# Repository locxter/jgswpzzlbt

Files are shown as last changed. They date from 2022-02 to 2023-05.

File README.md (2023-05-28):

# jgswpzzlbt

## Overview

> This project is **DEPRECATED**, therefore might not be on par with my current coding standards and will not receive any updates now or in the future.

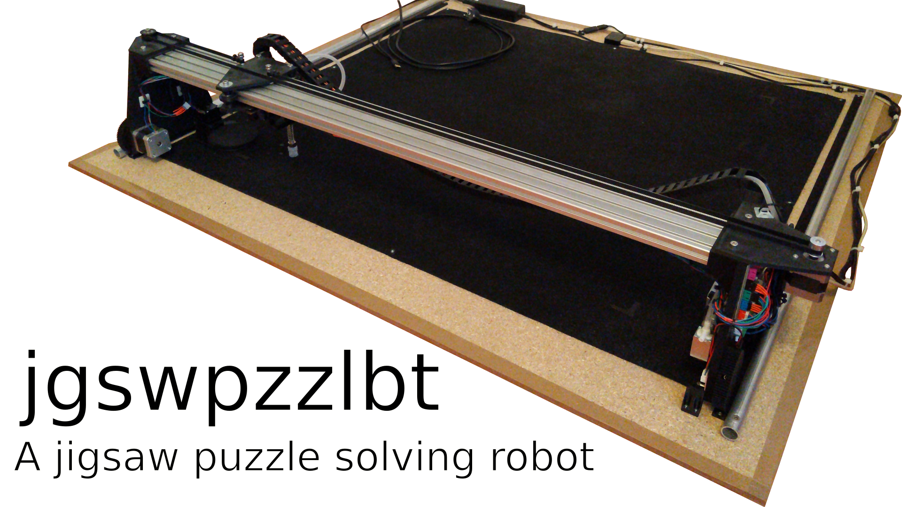
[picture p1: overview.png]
Overview image


This is a jigsaw puzzle solving robot I designed. It is programmed in C++ using OpenCV for image recognition and LibSerial for communicating with a custom Arduino firmware. For further information take a look at the overview video `overview.mp4` or the result images `6-part-result.jpeg` and `24-part-result.jpeg`.

## Dependencies

I generally try to minimize dependencies, but I'm a one man crew and can therefore only support Debian-based Linux distributions as I'm running one myself. Anyway, you need to have the following packages installed for everything to work properly:

- FreeCAD for editing and exporting the CAD files. Install it with `sudo apt install freecad`.
- A2Plus for assemblying the different components in FreeCAD. Install it via the integrated addon manager.
- freecad.gears for creating the needed gears in FreeCAD. Install it via the integrated addon manager.
- Arduino IDE as a way to compile the Arduino code. Install it with `sudo apt install arduino`.
- GCC, G++, GDB and CMake for building the C++ code. Install them with `sudo apt install build-essential gdb cmake`.
- OpenCV as the used computer vision library. Install it with `sudo apt install libopencv-dev`.
- LibSerial as the used serial communication library. Install it with `sudo apt install libserial-dev`.

## How it works

The process of solving a jigsaw puzzle automatically involves the following major steps:

1. Locating the somewhat randomly positioned parts.
2. Creating detailed pictures of all the parts.
3. Moving the parts to known positions inside a predefined matrix.
4. Locating each part in the provided overview picture of the puzzle.
5. Translating the digital positions to a real world ones.
6. Moving all the pieces to their final position.

## How to build it

jgswpzzlbt's mechanics mainly consist of a big 110x120cm chipboard, a 1m long 20x80mm aluminium extrusion and some custom 3D printed parts. For further information take a look at the assembly overview image `cad/assembly.png` as well as the assembly overview CAD model `cad/assembly.FCStd`. But please don't expect any parts to fit perfectly or be easy to assamble as only one prototype has been build so far.

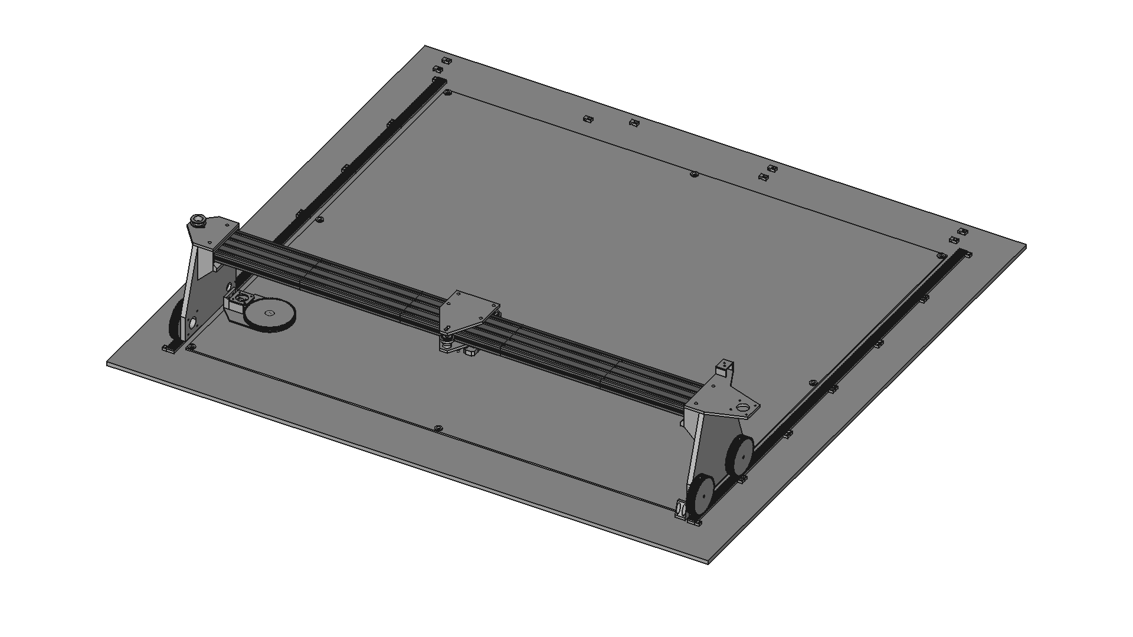
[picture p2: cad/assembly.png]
Assembly image


Below is a full bill of materials with German sources for all non printable parts:

| Quantity: | Item: | Source: |
| --- | --- | --- |
| 1 | MKS Base motherboard | [Amazon](https://www.amazon.de/Base-V1-6-RepRap-3D-Drucker-Steuerung/dp/B07G9K1T28) |
| 1 | HBV-1716WA USB camera | [Amazon](https://www.amazon.de/USB-Kameramodul-HBV-1716WA-Millionen-Weitwinkelobjektiv-OV2710-Chip/dp/B07QXXFGSM) |
| 1 | USB extension | [Amazon](https://www.amazon.de/deleyCON-Speed-Verl%C3%A4ngerungskabel-Stecker-Buchse/dp/B00WHZ7GBW) |
| 3 | NEMA 17 1.8deg stepper motor | [Amazon](https://www.amazon.de/STEPPERONLINE-Schrittmotor-63-74oz-4-Draht-Stepper/dp/B07MZJGNZN) |
| 1 | NEMA 11 1.8deg stepper motor | [Amazon](https://www.amazon.de/STEPPERONLINE-Schrittmotor-Bipolar-28x28x31mm-DRUCKER/dp/B07HHZQMDW) |
| 1 | Power supply | [Amazon](https://www.amazon.de/Netzteil-Netzadapter-Transformator-Kaltger%C3%A4testecker-Streifen/dp/B07FNMKTBL) |
| 1 | SG90 micro servo | [Amazon](https://www.amazon.de/ARCELI-Flugzeug-Zubeh%C3%B6r-Arduino-Hubschrauber/dp/B07MY2Y253) |
| 2 | Endstop | [Amazon](https://www.amazon.de/GTIWUNG-Mechanischer-Endschalter-3D-Drucker-Makerbot/dp/B07VWRS24K) |
| 1 | Vacuum pump | [Amazon](https://www.amazon.de/KSTE-Vakuumpumpe-Mikrovakuumpumpe-Mini-Luftpumpe-Behandlungsinstrument/dp/B08BJWLKBW) |
| 1 | Vacuum nozzle | [Amazon](https://www.amazon.de/SRJQXH-Pneumatischer-TS-M10-L80-11-Saugnapfhalter-Industrieller/dp/B098SCMZWY) |
| 1 | Vacuum valve | [Amazon](https://www.amazon.de/Magnetventil-%C3%96ffner-Fl%C3%BCssigkeit-Pneumatik-Elektroventil/dp/B0858Y2KSG) |
| 1 | Vacuum tubing | [Amazon](https://www.amazon.de/JBL-Luftschlauch-Länge-Durchmesser-Aquaschlauch/dp/B000H6SRMU) |
| 1 | Vacuum tubing connectors | [Amazon](https://www.amazon.de/Uniclife-Aquariumschl%C3%A4uche-Luftschlauchverbinder-Kunststoff-St%C3%BCck/dp/B07Q9Q9C8Y) |
| 1 | GT2 belt | [Amazon](https://www.amazon.de/OZUAR-Zahnriemen-3D-Drucker-Breite-Abstand/dp/B07D4GCYXW) |
| 1 | Cable ties and cable tie mounts | [Amazon](https://www.amazon.de/Hipeqia-Nylon-Kabelbinder-Kabelbinderhalter-Selbstklebend-Hitzebest%C3%A4ndig/dp/B08CL2JFCH) |
| 1 | Double sided tape | [Amazon](https://www.amazon.de/doppelseitiges-Klebeband-klebend-verschiedene-Breiten/dp/B00G6SCYCM) |
| 1 | Instant glue | [Amazon](https://www.amazon.de/Pattex-Sekundenkleber-L%C3%B6sungsmittelfreier-Gel-Kleber-Transparent/dp/B00O23B8IE) |
| 1 | Cable chain | [Amazon](https://www.amazon.de/Haobase-Plastic-Towline-Cable-Chain/dp/B06XKZ35VH) |
| 1 | Cables | [Amazon](https://www.amazon.de/Donau-Elektronik-GMBH-Original-Kupfer/dp/B01BI1G88C) |
| 1 | Pin header | [Amazon](https://www.amazon.de/IZOKEE-Männlich-Stiftleiste-Buchsenleiste-Lochrasterplatine/dp/B07DBY753C) |
| 1 | Jigsaw puzzle mat | [Amazon](https://www.amazon.de/maDDma-Bastelfilz-Meterware-Taschenfilz-Filzstoff/dp/B0797QR4LL) |
| 1 | 110x120cm chipboard 8mm | [Globus Baumarkt](https://www.globus-baumarkt.de/spanplatte-roh-8-mm) |
| 42 | 3x12mm TX10 wood screw | [Globus Baumarkt](https://www.globus-baumarkt.de/detail/index/sArticle/27670/fs/116194815/sCategory/47135) |
| 1 | Aluminium profile 20x80 I-type slot 5 1000mm | [Motedis](https://www.motedis.com/shop/Aluprofile/20-I-Typ-Nut-5/Aluprofil-20x80-I-Typ-Nut-5::3798.html) |
| 8 | M5 t-nut I-type groove 5 | [Motedis](https://www.motedis.com/shop/Nutprofil-Zubehoer/In-der-Nut/Nutenstein-Glatt-I-Typ-Nut-5-M5::5846.html) |
| 1 | GT2 motor pulley 20 teeth, 5mm bore | [Motedis](https://www.motedis.com/shop/Dynamik/Zahnriemen-und-Zahnraeder/GT2-Riemenscheibe-20-Zaehne-5mm-Bohrung-fuer-6mm-Riemen::4248.html) |
| 11 | 625 2RS ball bearing | [Motedis](https://www.motedis.com/shop/Dynamik-Basiselemente/Kugellager/Rillenkugellager/Rillenkugellager-625-2RS-5x16x5::4290.html) |
| 4 | DIN 912 M2x20 screw | [Schraubenkasten](https://www.schraubenkasten.de/din-912-mit-innensechskant/m2-8-8-galvanisch-verzinkt-zylinderschraube_200581_13656) |
| 4 | DIN 934 M2x0.4 nut | [Schraubenkasten](https://www.schraubenkasten.de/muttern/sechskantmutter/din-934/edelstahl-a2_202500_23008) |
| 4 | DIN 912 M2.5x8 screw | [Schraubenkasten](https://www.schraubenkasten.de/din-912-mit-innensechskant/m2-5-8-8-galvanisch-verzinkt-zylinderschraube_200582_13676) |
| 32 | DIN 912 M3x8 screw | [Schraubenkasten](https://www.schraubenkasten.de/din-912-mit-innensechskant/m3-8-8-galvanisch-verzinkt-zylinderschraube_200583_13715) |
| 18 | DIN 934 M3x0.5 nut | [Schraubenkasten](https://www.schraubenkasten.de/muttern/sechskantmutter/din-934/edelstahl-a2_202502_23016) |
| 12 | DIN 912 M5x14 screw | [Schraubenkasten](https://www.schraubenkasten.de/din-912-mit-innensechskant/m5-8-8-galvanisch-verzinkt-zylinderschraube_200585_13871) |
| 5 | DIN 912 M5x25 screw | [Schraubenkasten](https://www.schraubenkasten.de/din-912-mit-innensechskant/m5-8-8-galvanisch-verzinkt-zylinderschraube_200585_13883) |
| 3 | DIN 912 M5x50 screw | [Schraubenkasten](https://www.schraubenkasten.de/din-912-mit-innensechskant/m5-8-8-galvanisch-verzinkt-zylinderschraube_200585_13899) |
| 16 | DIN 934 M5 nut | [Schraubenkasten](https://www.schraubenkasten.de/muttern/sechskantmutter/din-934/edelstahl-a2_202504_23024) |
| 3 | DIN 7349 M5 washer | [Schraubenkasten](https://www.schraubenkasten.de/scheiben/unterlegscheiben/din-7349-schweren-spannstift/5-3-din-7349-scheiben-schrauben-mit-spannstifte-a2-edelstahl_203612_23840) |
| 9 | Cable clip | 3D printer |
| 8 | Cable tie mount | 3D printer |
| 1 | C axis gear | 3D printer |
| 1 | C axis motor mount | 3D printer |
| 1 | C axis turntable | 3D printer |
| 8 | Puzzle mat clamp | 3D printer |
| 1 | Vacuum tube fitting | 3D printer |
| 1 | X axis bottom carriage | 3D printer |
| 4 | X axis camera spacer | 3D printer |
| 1 | X axis motor mount | 3D printer |
| 1 | X axis pulley | 3D printer |
| 1 | X axis pulley mount | 3D printer |
| 1 | X axis pulley spacer | 3D printer |
| 3 | X axis roller | 3D printer |
| 6 | X axis roller spacer | 3D printer |
| 1 | X axis top carriage | 3D printer |
| 2 | Y axis carriage | 3D printer |
| 4 | Y axis gear | 3D printer |
| 1 | Y axis stop | 3D printer |
| 12 | Y axis track | 3D printer |
| 1 | Z axis carriage | 3D printer |
| 1 | Z axis gear | 3D printer |
| 1 | Z axis motor mount | 3D printer |

All parts were printed on my Sovol SV01 in standard PLA with a custom super fast profile. The following settings have been used with great success:

- 0.3mm layer height
- 0.6mm line width
- 1.2mm wall thickness
- 0.9mm top/bottom tickness
- 20% line infill
- 215°C nozzle temperature
- 60°C build plate temperature
- 75mm/s print speed (37.5mm/s for the initial layer, 75mm/s for infill, 37.5mm/s for walls, 120mm for travel)
- 100% cooling from the second layer on
- Zig zag support and 5mm raft, where necessary

## How to create a jigsaw puzzle

As this robot uses a special simplified type of jigsaw puzzles, you have to create the puzzles to solve with it yourself. You can simply use the given example puzzle by going to a photo shop (they offer a way better print quality than an average home printer), printing the file(s) `reference-with-cutting-lines.png` or in case of the 24 part version `reference-with-cutting-lines-NUMBER.png` in the common 15x10cm format and cutting it into pieces. But creating your own puzzle entirely isn't to difficult either. To do so you need to create a reference image of the whole jigsaw puzzle, a variant of this image with cutting lines as well as part images to help with labeling the cut parts later on. Then just print it out in your desired size and cut it into pieces. Keep in mind that the parts shouldn't get to small to work properly, 5x5cm per part is optimal.

## How to use it

After installing all the necessary tools and libraries mentioned above as well as building the hardware, you can flash the firmware to the MKS Base motherboard via the Arduino IDE and compile the camera calibration, manual control and main program with CMake. To do so simply create a build directory in each program's folder via `mkdir build`, move to it via `cd build` and run CMake via `cmake ..` followed by make via `make`. Then test the whole system with the manual control program via `./manual-control`. If everything works correctly, the next step is to perform the automatic camera calibration via `./camera-calibration`. Finally you can run the dang awesome thing with the main software via `./software` to solve some puzzles! Have fun ;)

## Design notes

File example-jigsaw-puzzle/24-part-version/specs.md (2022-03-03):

# Specs

- Columns: 6
- Rows: 4
- Width: 30cm
- Height: 20cm

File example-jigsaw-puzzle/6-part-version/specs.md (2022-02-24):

# Specs

- Columns: 3
- Rows: 2
- Width: 15cm
- Height: 10cm

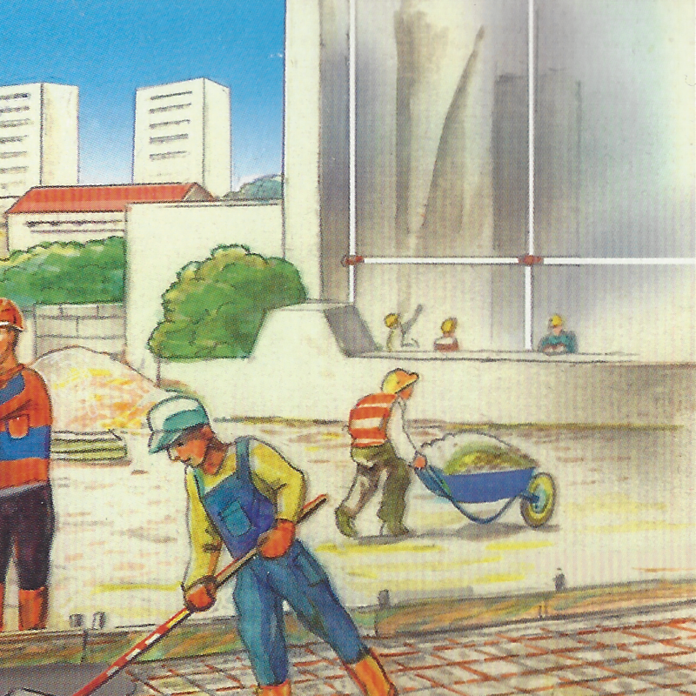
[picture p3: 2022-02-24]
example-jigsaw-puzzle/6-part-version/part-2-1.png

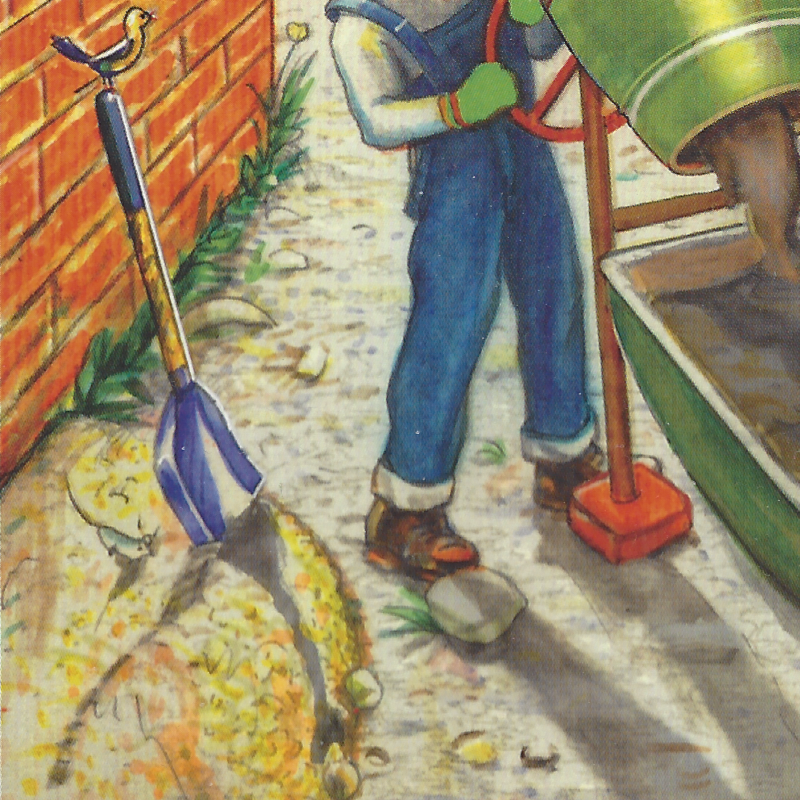
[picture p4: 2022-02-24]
example-jigsaw-puzzle/6-part-version/part-0-0.png

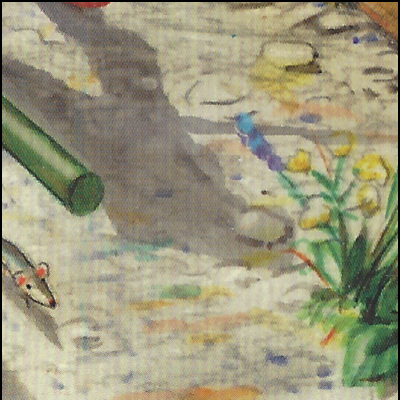
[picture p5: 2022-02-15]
example-jigsaw-puzzle/24-part-version/part-3-0.png

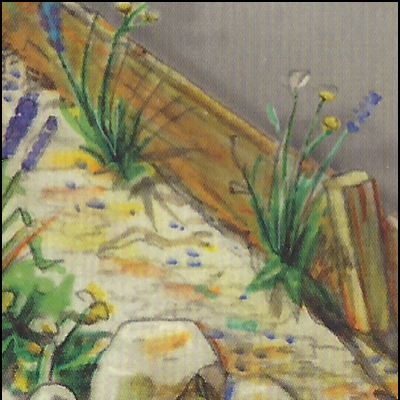
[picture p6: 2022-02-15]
example-jigsaw-puzzle/24-part-version/part-4-0.png

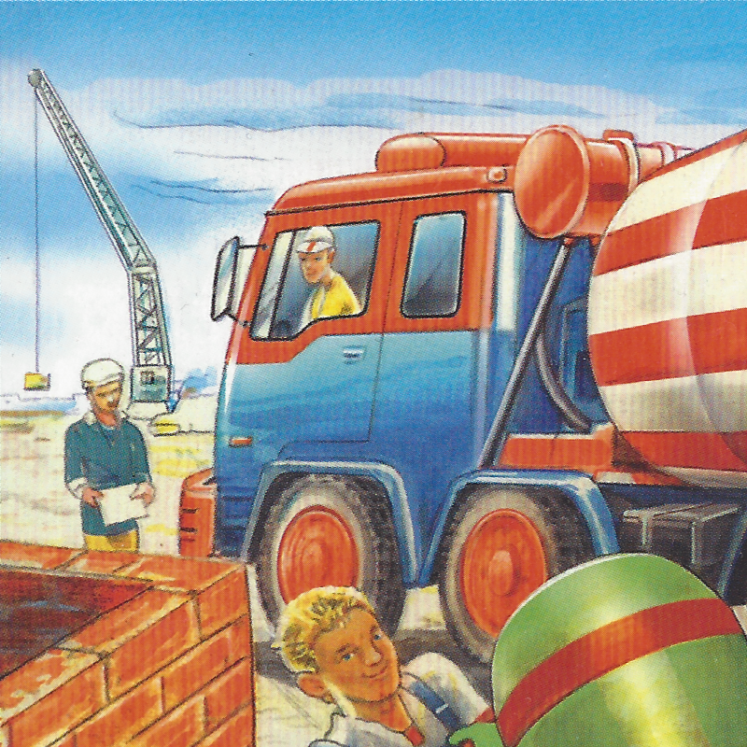
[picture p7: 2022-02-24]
example-jigsaw-puzzle/6-part-version/part-0-1.png

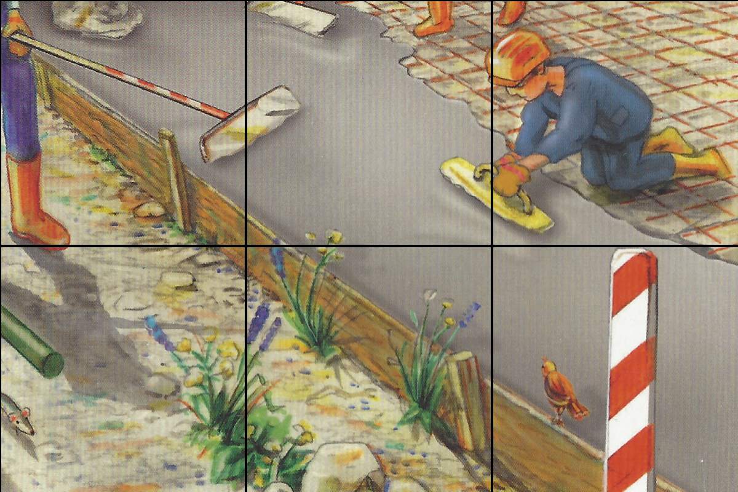
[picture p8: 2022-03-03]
example-jigsaw-puzzle/24-part-version/reference-with-cutting-lines-4.png

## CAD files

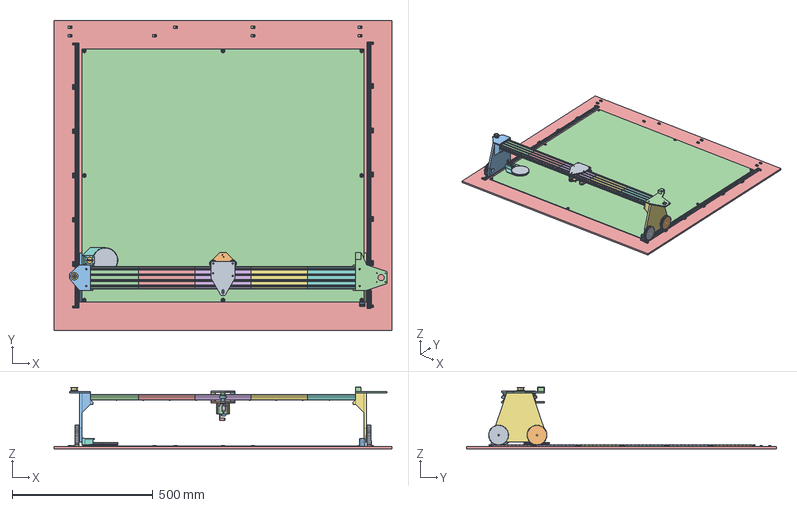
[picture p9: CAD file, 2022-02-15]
cad/assembly.FCStd
1200.0 x 1100.0 x 220.0 mm
y-axis-gear_001
y-axis-gear_002
y-axis-carriage_001
aluminium-profile1_001
aluminium-profile1_002
aluminium-profile1_003
aluminium-profile1_004
aluminium-profile1_005
y-axis-gear_003
y-axis-gear_004
x-axis-pulley-mount_001
x-axis-motor-mount_001
cable-clip_001
cable-clip_002
cable-clip_003
cable-clip_004
cable-clip_005
cable-clip_006
cable-clip_007
cable-clip_008
cable-clip_009
x-axis-pulley-spacer_001
x-axis-pulley_001
x-axis-roller_001
x-axis-roller_002
x-axis-roller_003
x-axis-roller-spacer_001
x-axis-roller-spacer_002
x-axis-roller-spacer_003
x-axis-roller-spacer_004
x-axis-roller-spacer_005
x-axis-roller-spacer_006
x-axis-top-carriage_001
x-axis-bottom-carriage_001
x-axis-camera-spacer_001
x-axis-camera-spacer_002
x-axis-camera-spacer_003
x-axis-camera-spacer_004
y-axis-track_001
y-axis-track_002
y-axis-track_003
y-axis-track_004
y-axis-track_005
y-axis-track_006
y-axis-track_007
y-axis-track_008
y-axis-track_009
y-axis-track_010
y-axis-track_011
y-axis-track_012
cable-tie-mount_001
cable-tie-mount_002
cable-tie-mount_003
cable-tie-mount_004
cable-tie-mount_005
cable-tie-mount_006
cable-tie-mount_007
cable-tie-mount_008
puzzle-mat-clamp_001
puzzle-mat-clamp_002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

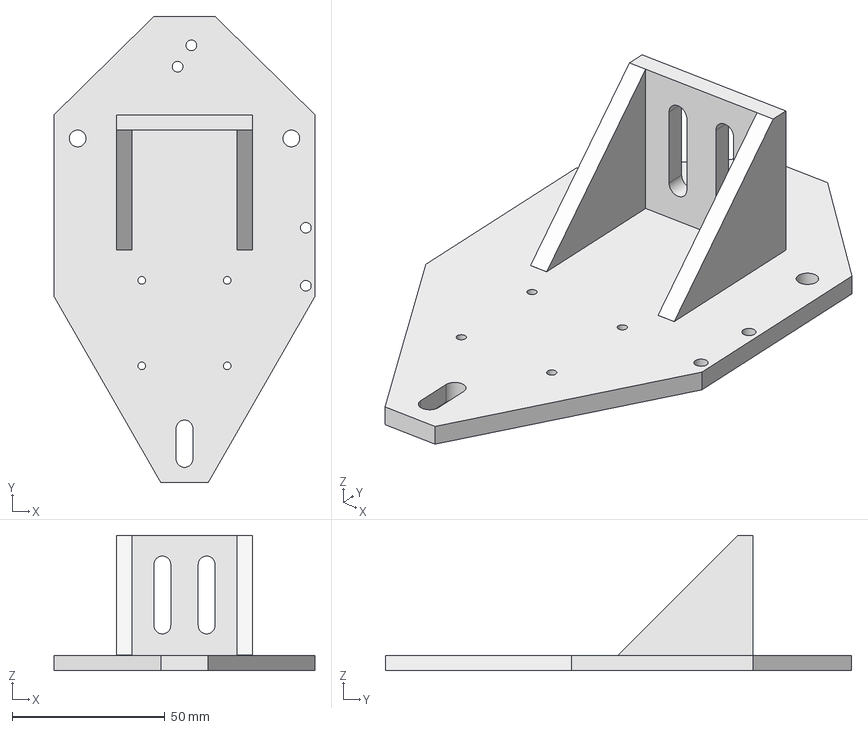
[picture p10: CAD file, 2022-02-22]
cad/x-axis-bottom-carriage.FCStd
85.5 x 152.7 x 44.3 mm

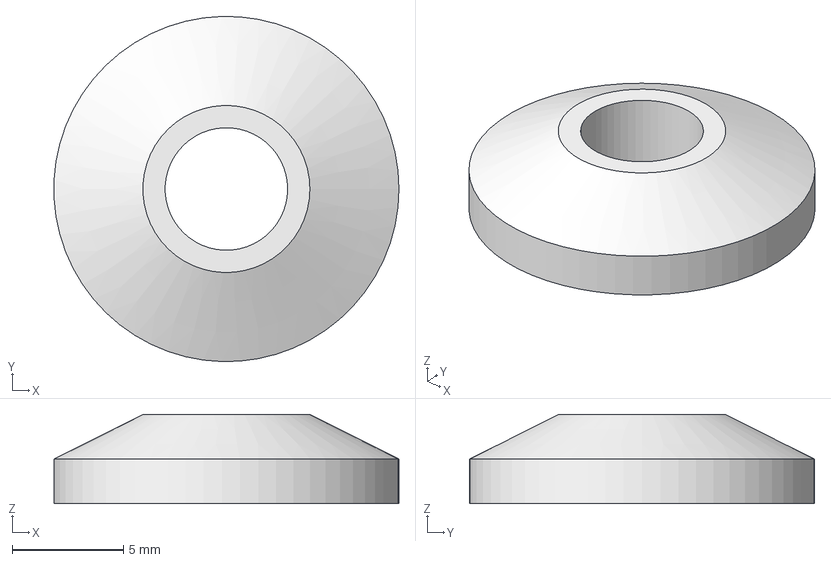
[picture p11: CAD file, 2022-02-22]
cad/x-axis-pulley-spacer.FCStd
15.5 x 15.5 x 4.00 mm

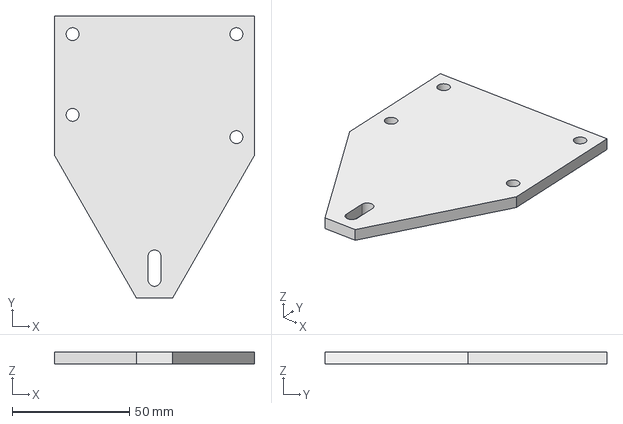
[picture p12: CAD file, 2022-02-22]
cad/x-axis-top-carriage.FCStd
85.5 x 120.5 x 5.00 mm

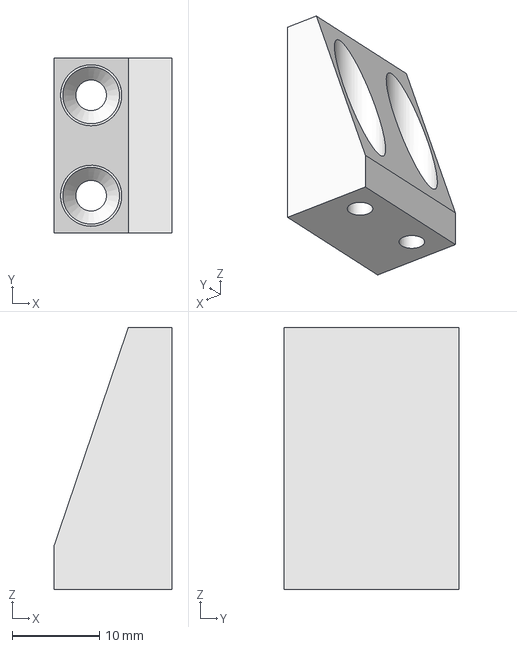
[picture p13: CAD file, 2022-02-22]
cad/y-axis-stop.FCStd
13.5 x 20.0 x 30.0 mm

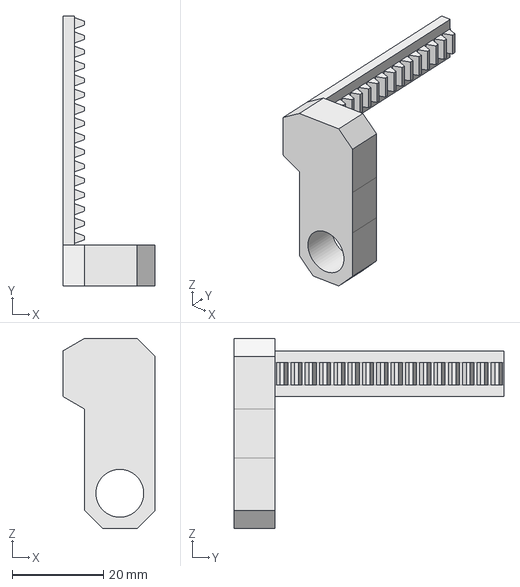
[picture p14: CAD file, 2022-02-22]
cad/z-axis-carriage.FCStd
20.2 x 59.3 x 41.8 mm

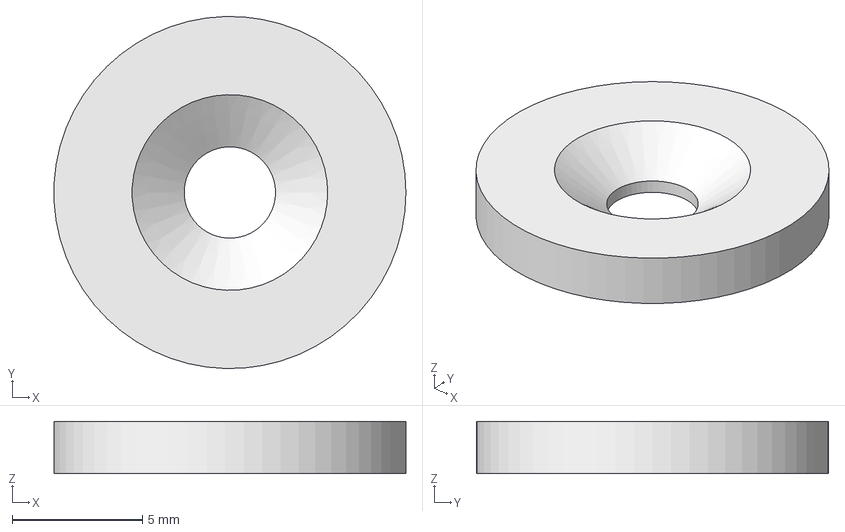
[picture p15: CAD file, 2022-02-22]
cad/puzzle-mat-clamp.FCStd
13.5 x 13.5 x 2.00 mm

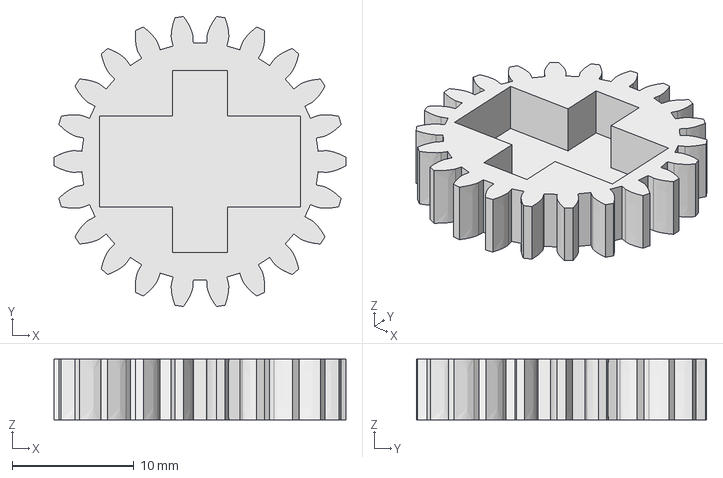
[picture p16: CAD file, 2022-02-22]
cad/z-axis-gear.FCStd
24.0 x 23.8 x 5.00 mm

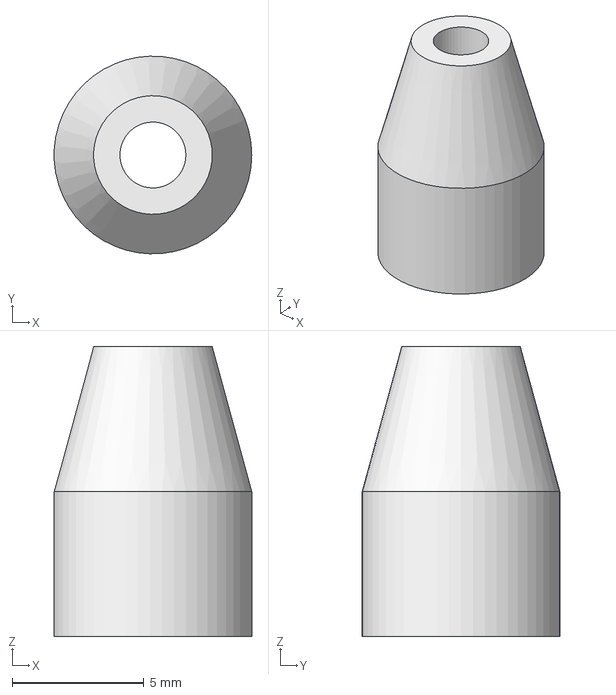
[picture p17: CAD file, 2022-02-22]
cad/x-axis-camera-spacer.FCStd
7.49 x 7.50 x 11.0 mm

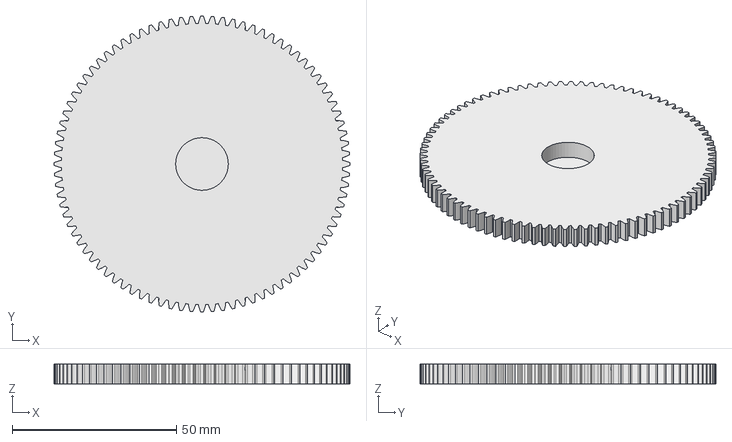
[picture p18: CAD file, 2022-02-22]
cad/c-axis-turntable.FCStd
90.0 x 90.0 x 6.00 mm

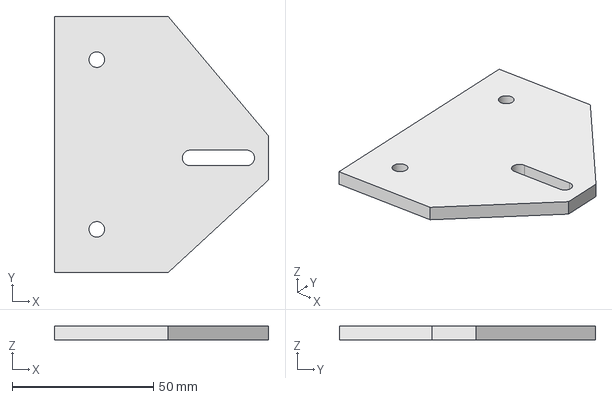
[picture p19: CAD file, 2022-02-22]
cad/x-axis-pulley-mount.FCStd
75.8 x 90.5 x 5.00 mm

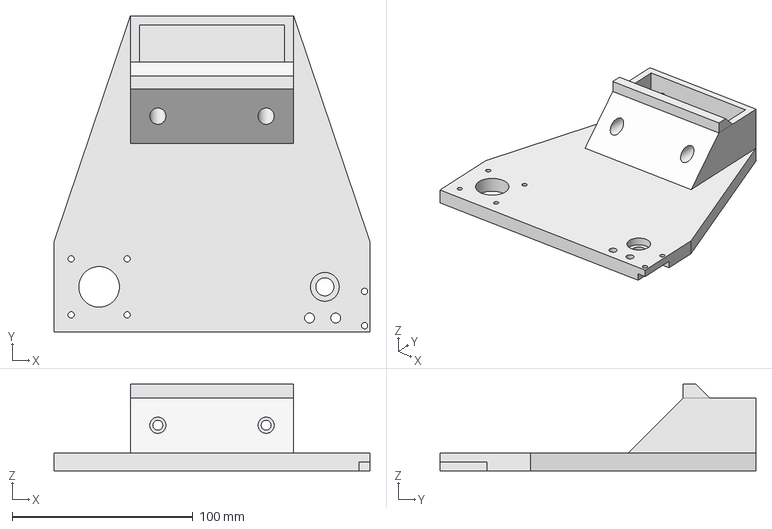
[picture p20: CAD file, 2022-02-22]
cad/y-axis-carriage.FCStd
175.0 x 175.0 x 48.0 mm

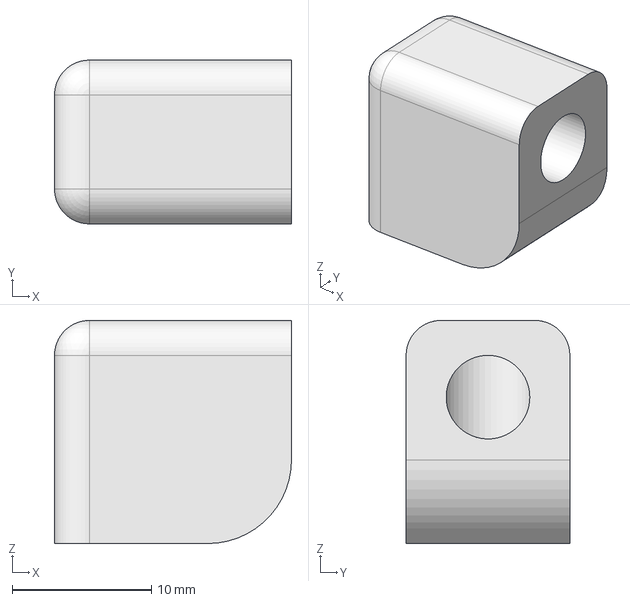
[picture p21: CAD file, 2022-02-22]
cad/vacuum-tube-fitting.FCStd
17.0 x 11.8 x 16.0 mm

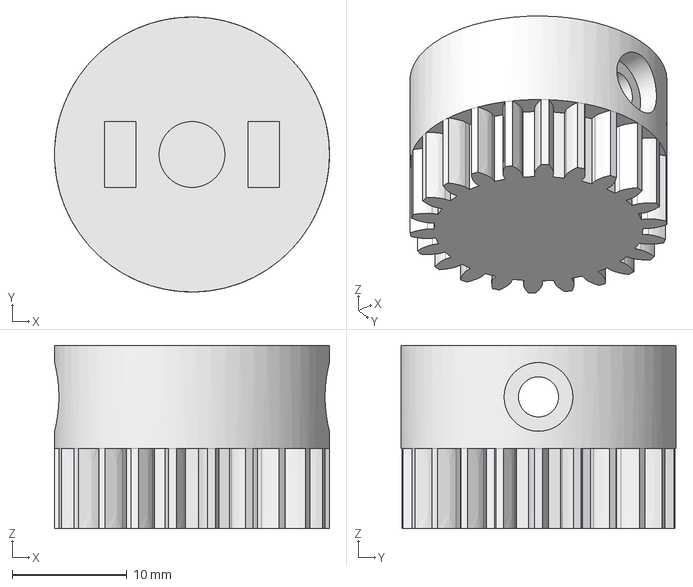
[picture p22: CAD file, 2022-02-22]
cad/c-axis-gear.FCStd
24.0 x 24.0 x 16.0 mm

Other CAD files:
cad/y-axis-track.FCStd
cad/y-axis-gear.FCStd
cad/x-axis-motor-mount.FCStd
cad/cable-tie-mount.FCStd
cad/aluminium-profile.stp
cad/c-axis-gear.stl
cad/c-axis-motor-mount.FCStd
cad/c-axis-motor-mount.stl
cad/c-axis-servo-arm.stl
cad/c-axis-turntable.stl
cad/cable-clip.FCStd
cad/cable-clip.stl
cad/puzzle-mat-clamp.stl
cad/vacuum-tube-fitting.stl
cad/x-axis-bottom-carriage.stl
cad/x-axis-camera-spacer.stl
cad/x-axis-motor-mount.stl
cad/x-axis-pulley-mount.stl
cad/x-axis-pulley-spacer.stl
cad/x-axis-pulley.FCStd
cad/x-axis-pulley.stl
cad/x-axis-roller-spacer.FCStd
cad/x-axis-roller-spacer.stl
cad/x-axis-roller.FCStd
cad/x-axis-roller.stl
cad/x-axis-top-carriage.stl
cad/y-axis-carriage.stl
cad/y-axis-gear.stl
cad/y-axis-stop.stl
cad/y-axis-track.stl
cad/z-axis-carriage.stl
cad/z-axis-gear.stl
cad/z-axis-motor-mount.FCStd
cad/z-axis-motor-mount.stl

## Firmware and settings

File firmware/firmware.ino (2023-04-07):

#include <Servo.h>

// Pins
const int X_AXIS_STP_PIN = A0;
const int X_AXIS_DIR_PIN = A1;
const int Y_AXIS_0_STP_PIN = A6;
const int Y_AXIS_0_DIR_PIN = A7;
const int Y_AXIS_1_STP_PIN = 46;
const int Y_AXIS_1_DIR_PIN = 48;
const int C_AXIS_STP_PIN = 26;
const int C_AXIS_DIR_PIN = 28;
const int X_AXIS_ENDSTOP_PIN = 3;
const int Y_AXIS_ENDSTOP_PIN = 14;
const int VACUUM_PUMP_PIN = 8;
const int VACUUM_VALVE_PIN = 10;

// Serial messages
const char AVAILABILITY_MESSAGE = 'R';
const char ERROR_MESSAGE = 'E';

// Servo object
Servo servo;

// Minimum x, y and c axis step intervals
const int X_AXIS_STEP_INTERVAL = 150;
const int Y_AXIS_STEP_INTERVAL = 750;
const int C_AXIS_STEP_INTERVAL = 200;

// Maximum x, y and z axis coordinates
const int X_AXIS_MAX = 825;
const int Y_AXIS_MAX = 725;
const int Z_AXIS_MAX = 90;

// X and y axis movement per rotation
const int X_AXIS_MOVEMENT_PER_ROTATION = 40;
const int Y_AXIS_MOVEMENT_PER_ROTATION = 220;

// Own functions
void homeAxis();
void moveXAxis(int x);
void moveYAxis(int y);
void moveZAxis(int z);
void moveCAxis(int angle);
void controlVacuumSystem(bool isOn);

// Setup function
void setup() {
    // More pins
    const int X_AXIS_ENA_PIN = 38;
    const int X_AXIS_MS1_PIN = 5;
    const int X_AXIS_MS2_PIN = 6;
    const int Y_AXIS_0_ENA_PIN = A2;
    const int Y_AXIS_0_MS1_PIN = A5;
    const int Y_AXIS_0_MS2_PIN = A4;
    const int Y_AXIS_1_ENA_PIN = A8;
    const int Y_AXIS_1_MS1_PIN = 22;
    const int Y_AXIS_1_MS2_PIN = 39;
    const int C_AXIS_ENA_PIN = 24;
    const int C_AXIS_MS1_PIN = A9;
    const int C_AXIS_MS2_PIN = A10;
    const int SERVO_PIN = 11;
    // Initiate pins and set them to their default states
    pinMode(X_AXIS_STP_PIN, OUTPUT);
    digitalWrite(X_AXIS_STP_PIN, LOW);
    pinMode(X_AXIS_DIR_PIN, OUTPUT);
    digitalWrite(X_AXIS_DIR_PIN, LOW);
    pinMode(X_AXIS_ENA_PIN, OUTPUT);
    digitalWrite(X_AXIS_ENA_PIN, LOW);
    pinMode(X_AXIS_MS1_PIN, OUTPUT);
    digitalWrite(X_AXIS_MS1_PIN, HIGH);
    pinMode(X_AXIS_MS2_PIN, OUTPUT);
    digitalWrite(X_AXIS_MS2_PIN, HIGH);
    pinMode(Y_AXIS_0_STP_PIN, OUTPUT);
    digitalWrite(Y_AXIS_0_STP_PIN, LOW);
    pinMode(Y_AXIS_0_DIR_PIN, OUTPUT);
    digitalWrite(Y_AXIS_0_DIR_PIN, HIGH);
    pinMode(Y_AXIS_0_ENA_PIN, OUTPUT);
    digitalWrite(Y_AXIS_0_ENA_PIN, LOW);
    pinMode(Y_AXIS_0_MS1_PIN, OUTPUT);
    digitalWrite(Y_AXIS_0_MS1_PIN, HIGH);
    pinMode(Y_AXIS_0_MS2_PIN, OUTPUT);
    digitalWrite(Y_AXIS_0_MS2_PIN, HIGH);
    pinMode(Y_AXIS_1_STP_PIN, OUTPUT);
    digitalWrite(Y_AXIS_1_STP_PIN, LOW);
    pinMode(Y_AXIS_1_DIR_PIN, OUTPUT);
    digitalWrite(Y_AXIS_1_DIR_PIN, LOW);
    pinMode(Y_AXIS_1_ENA_PIN, OUTPUT);
    digitalWrite(Y_AXIS_1_ENA_PIN, LOW);
    pinMode(Y_AXIS_1_MS1_PIN, OUTPUT);
    digitalWrite(Y_AXIS_1_MS1_PIN, HIGH);
    pinMode(Y_AXIS_1_MS2_PIN, OUTPUT);
    digitalWrite(Y_AXIS_1_MS2_PIN, HIGH);
    pinMode(C_AXIS_STP_PIN, OUTPUT);
    digitalWrite(C_AXIS_STP_PIN, LOW);
    pinMode(C_AXIS_DIR_PIN, OUTPUT);
    digitalWrite(C_AXIS_DIR_PIN, LOW);
    pinMode(C_AXIS_ENA_PIN, OUTPUT);
    digitalWrite(C_AXIS_ENA_PIN, LOW);
    pinMode(C_AXIS_MS1_PIN, OUTPUT);
    digitalWrite(C_AXIS_MS1_PIN, HIGH);
    pinMode(C_AXIS_MS2_PIN, OUTPUT);
    digitalWrite(C_AXIS_MS2_PIN, HIGH);
    pinMode(X_AXIS_ENDSTOP_PIN, INPUT);
    pinMode(Y_AXIS_ENDSTOP_PIN, INPUT);
    pinMode(VACUUM_PUMP_PIN, OUTPUT);
    digitalWrite(VACUUM_PUMP_PIN, LOW);
    pinMode(VACUUM_VALVE_PIN, OUTPUT);
    digitalWrite(VACUUM_VALVE_PIN, LOW);
    servo.attach(SERVO_PIN);
    // Open the serial connection
    Serial.begin(115200);
    // Home robot
    homeAxis();
}

// Main function
void loop() {
    // Check for new serial data
    if (Serial.available()) {
        // More serial messages
        const char X_AXIS_COMMAND = 'X';
        const char Y_AXIS_COMMAND = 'Y';
        const char Z_AXIS_COMMAND = 'Z';
        const char C_AXIS_COMMAND = 'C';
        const char VACUUM_SYSTEM_COMMAND = 'V';
        // Reade commands and their according parameters
        String input = Serial.readStringUntil('\n');
        char command = input.charAt(0);
        int commandParameter = input.substring(1).toInt();
        // Execute known commands or print an error
        switch (command) {
            case X_AXIS_COMMAND:
                moveXAxis(commandParameter);
                break;
            case Y_AXIS_COMMAND:
                moveYAxis(commandParameter);
                break;
            case Z_AXIS_COMMAND:
                moveZAxis(commandParameter);
                break;
            case C_AXIS_COMMAND:
                moveCAxis(commandParameter);
                break;
            case VACUUM_SYSTEM_COMMAND:
                if (commandParameter < 1) {
                    controlVacuumSystem(false);
                } else {
                    controlVacuumSystem(true);
                }
                break;
            default:
                Serial.print(ERROR_MESSAGE);
                Serial.print('\n');
                break;
        }
    }
}

// Function for homing the robot
void homeAxis() {
    // Variables for storing time before homing the x or y axis and success of that operation
    unsigned long startAxisHoming;
    bool success = true;
    // Move servo to a deactive coordinate
    if (servo.read() != Z_AXIS_MAX) {
        servo.write(Z_AXIS_MAX);
    }
    // Home the x axis
    startAxisHoming = millis();
    digitalWrite(X_AXIS_DIR_PIN, !digitalRead(X_AXIS_DIR_PIN));
    while (digitalRead(X_AXIS_ENDSTOP_PIN) == HIGH) {
        digitalWrite(X_AXIS_STP_PIN, HIGH);
        delayMicroseconds(10);
        digitalWrite(X_AXIS_STP_PIN, LOW);
        delayMicroseconds((2 * X_AXIS_STEP_INTERVAL) - 10);
        if (millis() - startAxisHoming > 60000) {
            success = false;
            break;
        }
    }
    digitalWrite(X_AXIS_DIR_PIN, !digitalRead(X_AXIS_DIR_PIN));
    // Home the y axis
    startAxisHoming = millis();
    digitalWrite(Y_AXIS_0_DIR_PIN, !digitalRead(Y_AXIS_0_DIR_PIN));
    digitalWrite(Y_AXIS_1_DIR_PIN, !digitalRead(Y_AXIS_1_DIR_PIN));
    while (digitalRead(Y_AXIS_ENDSTOP_PIN) == HIGH) {
        digitalWrite(Y_AXIS_0_STP_PIN, HIGH);
        digitalWrite(Y_AXIS_1_STP_PIN, HIGH);
        delayMicroseconds(10);
        digitalWrite(Y_AXIS_0_STP_PIN, LOW);
        digitalWrite(Y_AXIS_1_STP_PIN, LOW);
        delayMicroseconds((2 * Y_AXIS_STEP_INTERVAL) - 10);
        if (millis() - startAxisHoming > 60000) {
            success = false;
            break;
        }
    }
    digitalWrite(Y_AXIS_0_DIR_PIN, !digitalRead(Y_AXIS_0_DIR_PIN));
    digitalWrite(Y_AXIS_1_DIR_PIN, !digitalRead(Y_AXIS_1_DIR_PIN));
    // Check for homing error and print an according message
    if (success) {
        Serial.print(AVAILABILITY_MESSAGE);
        Serial.print('\n');
    } else {
        Serial.print(ERROR_MESSAGE);
        Serial.print('\n');
    }
}

// Function for controlling the x axis motor
void moveXAxis(int x) {
    // Variable to store current coordinate
    static int currentX = 0;
    // Limiting the parameter range
    if (x > X_AXIS_MAX) {
        x = X_AXIS_MAX;
    } else if (x < 0) {
        x = 0;
    }
    // Controlling the motor
    if (x != currentX) {
        int mmToGo;
        unsigned long long stepsToGo;
        // Calculating step interval related variables
        const long MAX_STEP_INTERVAL = (long) 100 * X_AXIS_STEP_INTERVAL;
        const long MIN_STEP_INTERVAL = X_AXIS_STEP_INTERVAL;
        const float STEP_INTERVAL_CHANGE = ((float) MAX_STEP_INTERVAL - MIN_STEP_INTERVAL) / 200;
        // Choosing a movement direction
        if (x > currentX) {
            mmToGo = x - currentX;
        } else if (x < currentX) {
            mmToGo = currentX - x;
            digitalWrite(X_AXIS_DIR_PIN, !digitalRead(X_AXIS_DIR_PIN));
        }
        stepsToGo = round(((float) mmToGo / X_AXIS_MOVEMENT_PER_ROTATION) * 3200);
        // Sending the step signals
        for (unsigned long long i = 0; i < stepsToGo; i++) {
            long stepInterval = MIN_STEP_INTERVAL - 10;
            // Slowing down at the start and end of the move
            if (i < 201) {
                stepInterval = round(MAX_STEP_INTERVAL - (i * STEP_INTERVAL_CHANGE)) - 10;
            } else if (i > (stepsToGo - 201)) {
                stepInterval = round(MIN_STEP_INTERVAL + ((i - (stepsToGo - 200)) * STEP_INTERVAL_CHANGE)) - 10;
            }
            digitalWrite(X_AXIS_STP_PIN, HIGH);
            delayMicroseconds(10);
            digitalWrite(X_AXIS_STP_PIN, LOW);
            delayMicroseconds(stepInterval);
        }
        // Resetting the movement direction
        if (x < currentX) {
            digitalWrite(X_AXIS_DIR_PIN, !digitalRead(X_AXIS_DIR_PIN));
        }
        // Updating the known x coordinate
        currentX = x;
    }
    // Printing an availability message
    Serial.print(AVAILABILITY_MESSAGE);
    Serial.print('\n');
}

// Function for controlling the y axis motor
void moveYAxis(int y) {
    // Defining variable to store current coordinate
    static int currentY = 0;
    // Limiting the parameter range
    if (y > Y_AXIS_MAX) {
        y = Y_AXIS_MAX;
    } else if (y < 0) {
        y = 0;
    }
    // Controlling the motor
    if (y != currentY) {
        int mmToGo;
        unsigned long long stepsToGo;
        // Choosing a movement direction
        if (y > currentY) {
            mmToGo = y - currentY;
        } else if (y < currentY) {
            mmToGo = currentY - y;
            digitalWrite(Y_AXIS_0_DIR_PIN, !digitalRead(Y_AXIS_0_DIR_PIN));
            digitalWrite(Y_AXIS_1_DIR_PIN, !digitalRead(Y_AXIS_1_DIR_PIN));
        }
        stepsToGo = round(((float) mmToGo / Y_AXIS_MOVEMENT_PER_ROTATION) * 3200);
        // Sending the step signals
        for (unsigned long long i = 0; i < stepsToGo; i++) {
            long stepInterval = Y_AXIS_STEP_INTERVAL - 10;
            // Slowing down at the start and end of the move
            if (i < 201 || i > (stepsToGo - 201)) {
                stepInterval = (2 * Y_AXIS_STEP_INTERVAL) - 10;
            }
            digitalWrite(Y_AXIS_0_STP_PIN, HIGH);
            digitalWrite(Y_AXIS_1_STP_PIN, HIGH);
            delayMicroseconds(10);
            digitalWrite(Y_AXIS_0_STP_PIN, LOW);
            digitalWrite(Y_AXIS_1_STP_PIN, LOW);
            delayMicroseconds(stepInterval);
        }
        // Resetting the movement direction
        if (y < currentY) {
            digitalWrite(Y_AXIS_0_DIR_PIN, !digitalRead(Y_AXIS_0_DIR_PIN));
            digitalWrite(Y_AXIS_1_DIR_PIN, !digitalRead(Y_AXIS_1_DIR_PIN));
        }
        // Updating the known y coordinate
        currentY = y;
    }
    // Printing an availability message
    Serial.print(AVAILABILITY_MESSAGE);
    Serial.print('\n');
}

// Function for controlling the x axis servo
void moveZAxis(int z) {
    // Limiting the parameter range
    if (z > Z_AXIS_MAX) {
        z = Z_AXIS_MAX;
    } else if (z < 0) {
        z = 0;
    }
    // Controlling the servo
    if (z != servo.read()) {
        servo.write(z);
    }
    // Printing an availability message
    Serial.print(AVAILABILITY_MESSAGE);
    Serial.print('\n');
}

// Function for controlling the c axis motor
void moveCAxis(int angle) {
    unsigned long long stepsToGo = round((abs(angle) / 90.0) * 3200);
    // Calculating step interval related variables
    const long MAX_STEP_INTERVAL = 100 * C_AXIS_STEP_INTERVAL;
    const long MIN_STEP_INTERVAL = C_AXIS_STEP_INTERVAL;
    const float STEP_INTERVAL_CHANGE = ((float) MAX_STEP_INTERVAL - MIN_STEP_INTERVAL) / 200;
    // Choosing a movement direction
    if (angle < 0) {
        digitalWrite(C_AXIS_DIR_PIN, !digitalRead(C_AXIS_DIR_PIN));
    }
    // Sending the step signals
    for (unsigned long long i = 0; i < stepsToGo; i++) {
        long stepInterval = MIN_STEP_INTERVAL - 10;
        // Slowing down at the start and end of the move
        if (i < 201) {
            stepInterval = round(MAX_STEP_INTERVAL - (i * STEP_INTERVAL_CHANGE)) - 10;
        } else if (i > (stepsToGo - 201)) {
            stepInterval = round(MIN_STEP_INTERVAL + ((i - (stepsToGo - 200)) * STEP_INTERVAL_CHANGE)) - 10;
        }
        digitalWrite(C_AXIS_STP_PIN, HIGH);
        delayMicroseconds(10);
        digitalWrite(C_AXIS_STP_PIN, LOW);
        delayMicroseconds(stepInterval);
    }
    // Resetting the movement direction
    if (angle < 0) {
        digitalWrite(C_AXIS_DIR_PIN, !digitalRead(C_AXIS_DIR_PIN));
    }
    // Printing an availability message
    Serial.print(AVAILABILITY_MESSAGE);
    Serial.print('\n');
}

// Function for controlling the vacuum system
void controlVacuumSystem(bool isOn) {
    // Controlling the vacuum system
    if (isOn) {
        digitalWrite(VACUUM_VALVE_PIN, LOW);
        digitalWrite(VACUUM_PUMP_PIN, HIGH);
    } else {
        digitalWrite(VACUUM_VALVE_PIN, HIGH);
        digitalWrite(VACUUM_PUMP_PIN, LOW);
    }
    // Printing an availability message
    Serial.print(AVAILABILITY_MESSAGE);
    Serial.print('\n');
}

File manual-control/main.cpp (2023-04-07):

#include "lib/libserial-helpers.hpp"
#include "lib/opencv-helpers.hpp"
#include <iostream>

// Main function
int main(int argc, char** argv) {
    // Check for the right number of command line arguments
    if (argc == 4) {
        // Variables for command line arguments
        const std::string CAMERA_CALIBRATION_FILE = argv[1];
        const int CAMERA_ID = std::stoi(argv[2]);
        const std::string SERIAL_PORT = argv[3];
        const std::string WINDOW_NAME = "jgswpzzlbt manual control";
        // Robot axis maximums
        const int X_AXIS_MAX = 825;
        const int Y_AXIS_MAX = 725;
        const int Z_AXIS_MAX = 90;
        // Objects for robot communication
        cv::VideoCapture camera;
        cv::Mat cameraMatrix;
        cv::Mat distortionCoefficients;
        cv::FileStorage cameraCalibration;
        LibSerial::SerialStream serial;
        std::string response;
        // Initialize robot
        cameraCalibration.open("camera-calibration.xml", cv::FileStorage::READ);
        if (cameraCalibration.isOpened()) {
            std::cout << "Opened camera calibration successfully." << std::endl;
        } else {
            std::cout << "Failed to open camera calibration." << std::endl;
            return 1;
        }
        cameraCalibration["camera-matrix"] >> cameraMatrix;
        cameraCalibration["distortion-coefficients"] >> distortionCoefficients;
        cameraCalibration.release();
        camera.open(CAMERA_ID, cv::CAP_V4L);
        if (camera.isOpened()) {
            std::cout << "Opened camera successfully." << std::endl;
        } else {
            std::cout << "Failed to open camera." << std::endl;
            return 1;
        }
        camera.set(cv::CAP_PROP_FOURCC, cv::VideoWriter::fourcc('M', 'J', 'P', 'G'));
        camera.set(cv::CAP_PROP_FRAME_WIDTH, 1920);
        camera.set(cv::CAP_PROP_FRAME_HEIGHT, 1080);
        camera.set(cv::CAP_PROP_FPS, 25);
        camera.set(cv::CAP_PROP_BUFFERSIZE, 1);
        serial.Open(SERIAL_PORT);
        if (serial.IsOpen()) {
            std::cout << "Opened serial port successfully." << std::endl;
        } else {
            std::cout << "Unable to open serial port." << std::endl;
            return 1;
        }
        serial.SetBaudRate(LibSerial::BaudRate::BAUD_115200);
        std::getline(serial, response);
        if (response.at(0) == AVAILABILITY_MESSAGE) {
            std::cout << "Robot homed successfully." << std::endl;
        } else {
            std::cout << "Homing of the robot failed." << std::endl;
            return 1;
        }
        // Display a small help at start
        cv::namedWindow(WINDOW_NAME);
        showImage(
            WINDOW_NAME,
            drawText(
                cv::Mat::zeros(cv::Size(1280, 720), CV_8UC3),
                "This program is fully keyboard driven. Here is a full list of all available actions:\nQ: Quit the "
                "program\nF: Save the current frame\n1 to 9: Set the value change to 1, 5, 10, 25, 50, 75, 100, 250 or "
                "500\nD: Increase x axis coordinate\nA: Decrease x axis coordinate\nW: Increase y axis coordinate\nS: "
                "Decrease y axis coordinate\nUP ARROW: Increase z axis coordinate\nDOWN ARROW : Decrease z axis "
                "coordinate\nRIGHT ARROW: Increase c axis coordinate\nLEFT ARROW: Decrease c axis coordinate\nT: Turn "
                "vacuum system on\nG: Turn vacuum system off\nR: Indicate that the next operation can be performed"));
        // Endless frame capturing, displaying and communcation loop
        while (true) {
            // Image containers and variable for storing the key pressed
            cv::Mat rawFrame;
            cv::Mat resizedFrame;
            cv::Mat annotatedFrame;
            int keyPressed;
            // Coordinate storage and variable for storing the increment/decrement
            static int x = 0;
            static int y = 0;
            static int z = 90;
            static bool isVacuumOn = false;
            static int valueChange = 10;
            // Show a frame
            rawFrame = capturePicture(camera, cameraMatrix, distortionCoefficients);
            cv::resize(rawFrame, resizedFrame, cv::Size(1280, 720));
            annotatedFrame =
                drawText(resizedFrame, "Value change: " + std::to_string(valueChange) + " X: " + std::to_string(x) +
                                           " Y: " + std::to_string(y) + " Z: " + std::to_string(z) +
                                           " V: " + std::to_string(isVacuumOn));
            cv::imshow(WINDOW_NAME, annotatedFrame);
            // Fetch user input
            keyPressed = cv::waitKey(1000 / 25);
            // Quit when Q is pressed
            if (keyPressed == 113) {
                break;
            }
            // Save the current frame when F is pressed
            else if (keyPressed == 102) {
                savePicture(rawFrame, "manual-control");
            }
            // Set the value change to one of the presets
            else if (keyPressed == 49) {
                valueChange = 1;
                std::cout << "Value change: 1" << std::endl;
            } else if (keyPressed == 50) {
                valueChange = 5;
                std::cout << "Value change: 5" << std::endl;
            } else if (keyPressed == 51) {
                valueChange = 10;
                std::cout << "Value change: 10" << std::endl;
            } else if (keyPressed == 52) {
                valueChange = 25;
                std::cout << "Value change: 25" << std::endl;
            } else if (keyPressed == 53) {
                valueChange = 50;
                std::cout << "Value change: 50" << std::endl;
            } else if (keyPressed == 54) {
                valueChange = 75;
                std::cout << "Value change: 75" << std::endl;
            } else if (keyPressed == 55) {
                valueChange = 100;
                std::cout << "Value change: 100" << std::endl;
            } else if (keyPressed == 56) {
                valueChange = 250;
                std::cout << "Value change: 250" << std::endl;
            } else if (keyPressed == 57) {
                valueChange = 500;
                std::cout << "Value change: 500" << std::endl;
            }
            // Increase x axis coordinate when D is pressed
            else if (keyPressed == 100) {
                x += valueChange;
                if (x > X_AXIS_MAX) {
                    x = X_AXIS_MAX;
                }
                sendCommand(serial, X_AXIS_COMMAND, x);
                std::cout << "X: " << x << std::endl;
            }
            // Decrease x axis coordinate when A is pressed
            else if (keyPressed == 97) {
                x -= valueChange;
                if (x < 0) {
                    x = 0;
                }
                sendCommand(serial, X_AXIS_COMMAND, x);
                std::cout << "X: " << x << std::endl;
            }
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

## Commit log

2021-02-16 Addes files via upload
    [assembly.scad, c-axis-motor-mount.scad, c-axis-motor-mount.stl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]
2021-02-18 Build the firmware and updated some CAD files.
    [assembly.scad, x-axis-pulley-spacer.scad, x-axis-pulley-spacer.stl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]
2021-02-27 Improved some CAD files and add a light control to the firmware.
    [assembly.scad, c-axis-servo-mount.scad, c-axis-servo-mount.stl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]
2021-03-24 Created a live camera viewer as well as overview picture.
    [assembly.scad, c-axis-motor-mount.scad, c-axis-servo-arm.scad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]
2021-04-27 Added a cable chain and updated some other minor stuff.
    [assembly.scad, c-axis-motor-mount.scad, c-axis-motor-mount.stl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]
2021-05-01 Merged the standalone BOM into the README.
2021-05-15 Added camera calibration functionality.
2021-05-24 Fixed some bugs and added a manual control program.
    [firmware.ino, main.cpp]
2021-05-28 Updated the REDME to my current software setup.
2021-09-19 Moved all the CAD files to FreeCAD and incorporated major improvementss of the hardware as well as software.
    [aluminium-profile.stp, assembly.FCStd, assembly.scad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]
2021-09-23 Did some minor tweaks to the CAD files.
    [assembly.FCStd, c-axis-servo-arm.FCStd, c-axis-servo-mount.FCStd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]
2021-11-20 Totally redesigned the y and z axis as well as the manual control program.
    [assembly.FCStd, c-axis-servo-arm.FCStd, c-axis-servo-mount.FCStd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]
2021-11-21 Updated to assembly file to accommodate the latest changes.
    [assembly.FCStd]
2021-12-17 Added a y axis endstop, wrote a calibration program and started working on the main control software.
    [assembly.FCStd, vacuum-tube-guide.FCStd, vacuum-tube-guide.stl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]
2021-12-29 Updated everything to accommodate my switch to plain Ubuntu and implemented part detection at pickup.
    [assembly.FCStd, vacuum-tube-guide.FCStd, vacuum-tube-guide.stl]
2022-02-15 Totally reworked the z and c axis.
    [assembly.FCStd, c-axis-gear.FCStd, c-axis-motor-mount.FCStd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]
2022-02-20 Fixed some erros so that it finally solves some basic puzzlesgit add .!
    [firmware.ino, main.cpp]
2022-02-22 Added STLs.
    [c-axis-gear.FCStd, c-axis-gear.stl, c-axis-motor-mount.FCStd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]
2022-02-24 Small improvements for better low light capabilities and more accurate y axis movements.
2022-02-26 Switched back to Debian ending my distro hopping.
2022-02-26 Removed the 24 part example puzzle as the parts were just to small and replaced it with a well working 15 part version.
    [main.cpp]
2022-02-27 Fixed a small mistake and added my VSCodium extensions to the dependencies.
    [main.cpp]
2022-03-03 The 15 part version turned out to be unreliable as well, so I replaced it with a now actually well working 24 part version with way bigger parts.
    [main.cpp]
2022-03-12 Reworked the software structure and made some overall style improvements.
    [firmware.ino, main.cpp]
2022-06-07 Fixed some stupid mistakes.
    [main.cpp]
2022-07-06 Reworked some of yesterday's changes.
    [firmware.ino]
2022-07-10 Fixed some more minor mistakes.
    [main.cpp]
2022-07-12 Revert "Added some more safety checks."
    This reverts commit 8f68a7fb801a20dd4974c02bfe6e75622e11b0d6.
    [firmware.ino, main.cpp]
2022-09-11 Switched back to Ubuntu due to hardware compatibility.
2022-10-16 Switched back to good old Linux Mint.
2022-12-13 Fixed a small mistake.
    [main.cpp]
